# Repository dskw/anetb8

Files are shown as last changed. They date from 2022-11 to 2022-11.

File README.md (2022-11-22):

# Rebuild of the Anet A8 with 2020 extrusions


# Extrusions
* 1x 140mm
* 1x 220mm
* 2x 440mm
* 2x 400mm
* 4x 420mm

# Hardware
* Geetech GT2560 https://www.geeetech.com/wiki/index.php/GT2560
* Buwei 3.3V 1 Channel Relais
* 12V 30A PSU (removed the top plate that holds the fan)
* Noctua NF-A6x25 (60mm)
* RepRapDiscount Full Graphic Smart Controller
* Raspberry Pi 3 B
* deleyCON 1x CAT6a MINI Keystone Jack Modul
* selfmade short 90° usb cables (Pi -> MCU, Pi -> USB Backport)
* selfmade short 90° LAN cable (Pi -> deleyCON)
* 10x15mm drag chain 1 meter
* E3D V6 Clone
* BMG dual gear extruder

All parts are printed in ABS with 5 top/bottom layers and 4 perimeters for maximum stability. (Voron settings)

Additional STLs:
* Printhead: https://www.thingiverse.com/thing:3453289
* Fanduct: https://www.thingiverse.com/thing:2121279 (Mistral_V2.1_Leo_N)

# Printer


# Electronis



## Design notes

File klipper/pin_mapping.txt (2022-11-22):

//
// Limit Switches
//
#define X_MIN_PIN                             22 -> PA0
#define X_MAX_PIN                             24 -> PA2
#define Y_MIN_PIN                             26 -> PA4
#define Y_MAX_PIN                             28 -> PA6
#define Z_MIN_PIN                             30 -> PC7

#define SERVO0_PIN                        11 -> PB5
#define Z_MAX_PIN                         32 -> PC5

//
// Steppers
//
#define X_STEP_PIN                            25 -> PA3
#define X_DIR_PIN                             23 -> PA1
#define X_ENABLE_PIN                          27 -> PA5

#define Y_STEP_PIN                            31 -> PC6
#define Y_DIR_PIN                             33 -> PC4
#define Y_ENABLE_PIN                          29 -> PA7

#define Z_STEP_PIN                            37 -> PC0
#define Z_DIR_PIN                             39 -> PG2
#define Z_ENABLE_PIN                          35 -> PC2

#define E0_STEP_PIN                           43 -> PL6
#define E0_DIR_PIN                            45 -> PL4
#define E0_ENABLE_PIN                         41 -> PG0

#define E1_STEP_PIN                           49 -> PL0
#define E1_DIR_PIN                            47 -> PL2
#define E1_ENABLE_PIN                         48 -> PL1

//
// Temperature Sensors
//
#define TEMP_0_PIN                             8 -> PH5
#define TEMP_1_PIN                             9 -> PH6
#define TEMP_BED_PIN                          10 -> PB4

//
// Heaters / Fans
//
#define HEATER_0_PIN                           2 -> PE4
#define HEATER_1_PIN                           3 -> PE5
#define HEATER_BED_PIN                         4 -> PG5
#define FAN_PIN                              7 -> PH4

//
// Misc. Functions
//
#define SDSS                                  53 -> PB0
#define LED_PIN                               13 -> PB7
#define PS_ON_PIN                             12 -> PB6
#define SUICIDE_PIN                           54  -> PF0 // Must be enabled at startup to keep power flowing
#define KILL_PIN                              -1

#if HAS_WIRED_LCD

  #define BEEPER_PIN                          18 -> PD3

  #if IS_NEWPANEL

    #if ENABLED(MKS_MINI_12864)
      #define DOGLCD_A0                        5
      #define DOGLCD_CS                       21
      #define BTN_EN1                         40
      #define BTN_EN2                         42
    #elif ENABLED(FYSETC_MINI_12864)
      // Disconnect EXP2-1 and EXP2-2, otherwise future firmware upload won't work.
      #define DOGLCD_A0                       20
      #define DOGLCD_CS                       17

      #define NEOPIXEL_PIN                    21
      #define BTN_EN1                         42
      #define BTN_EN2                         40

      #define LCD_RESET_PIN                   16

      #define LCD_CONTRAST_INIT              220

      #define LCD_BACKLIGHT_PIN               -1
    #else
      #define LCD_PINS_RS                     20
      #define LCD_PINS_ENABLE                 17
      #define LCD_PINS_D4                     16
      #define LCD_PINS_D5                     21
      #define LCD_PINS_D6                      5
      #define LCD_PINS_D7                      6
      #define BTN_EN1                         42
      #define BTN_EN2                         40
    #endif

    #define BTN_ENC                           19
    #define SD_DETECT_PIN                     38

  #else                                           // !IS_NEWPANEL

    #define SHIFT_CLK_PIN                     38
    #define SHIFT_LD_PIN                      42
    #define SHIFT_OUT_PIN                     40
    #define SHIFT_EN_PIN                      17

    #define LCD_PINS_RS                       16
    #define LCD_PINS_ENABLE                    5
    #define LCD_PINS_D4                        6
    #define LCD_PINS_D5                       21
    #define LCD_PINS_D6                       20
    #define LCD_PINS_D7                       19

    #if ENABLED(REPRAP_DISCOUNT_FULL_GRAPHIC_SMART_CONTROLLER)
      #define BTN_ENC_EN             LCD_PINS_D7  // Detect the presence of the encoder
    #endif

    #define SD_DETECT_PIN                     -1

  #endif // !IS_NEWPANEL

#endif // HAS_WIRED_LCD

  #define SERVO0_PIN  32

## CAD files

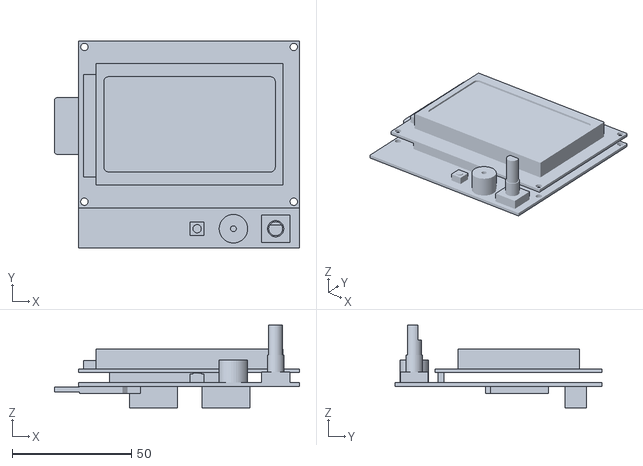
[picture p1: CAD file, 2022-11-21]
source/Full_Graphic_Smart_Controller.STL
102.9 x 86.8 x 34.7

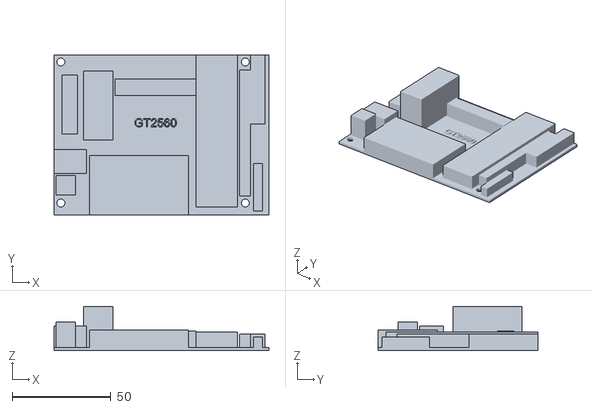
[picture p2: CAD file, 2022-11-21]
source/gt2560.stl
109.0 x 81.0 x 22.5

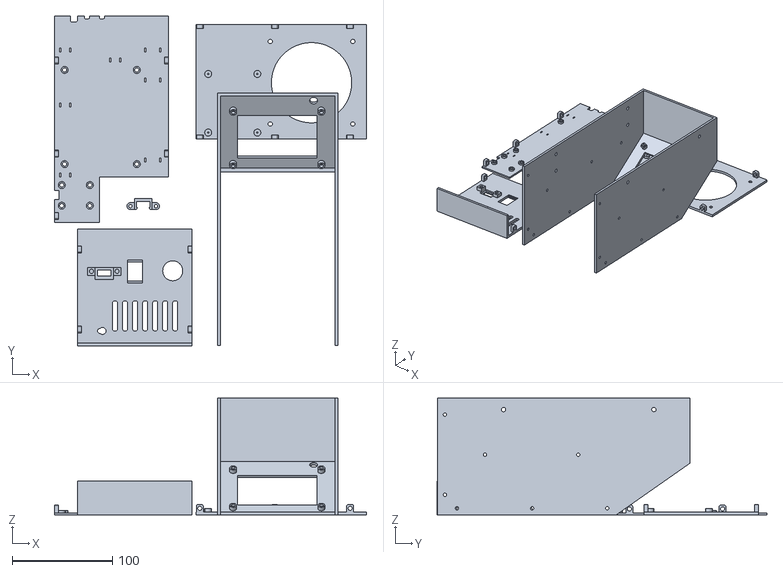
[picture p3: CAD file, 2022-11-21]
stl/anetb8_electronics.stl
311.6 x 329.2 x 116.6

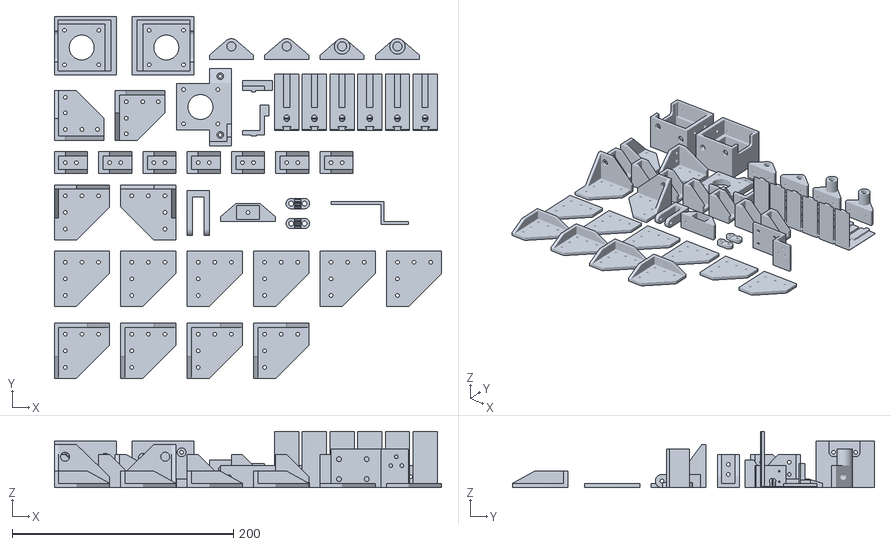
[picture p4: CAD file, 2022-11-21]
stl/anetb8.stl
350.0 x 327.0 x 51.0

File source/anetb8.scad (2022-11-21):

include <libsko.scad>;
//include <SCxxUU-SCxxLUU_v05.scad>

/*
Extrusions
 2x 440
 2x 345 -> 140, 220
 2x 400
 4x 420
 
Rods
 2x 436
 4x 380
 
Lead Screws
2x 345
2x 400
1x 150
*/

RED = [1, 0.3, 0.3];

module Rod(length=10) color("lightgray") render() translate([4, 4, 0]) cylinder(h=length, d=8, $fn=32);

module cornercover() render()
{
    height = 4;
    difference()
    {
        rotate([0,0,-90]) hull()
        {
            cube([50,20,height]);
            cube([20,50,height]);
        }
        translate([25,-10,-0.01]) cylinder(r=M3, h=height+0.02, $fn=32);
        translate([40,-10,-0.01]) cylinder(r=M3, h=height+0.02, $fn=32);
        translate([10,-10,-0.01]) cylinder(r=M3, h=height+0.02, $fn=32);
        translate([10,-25,-0.01]) cylinder(r=M3, h=height+0.02, $fn=32);
        translate([10,-40,-0.01]) cylinder(r=M3, h=height+0.02, $fn=32);
    }
}

module cornercover_foot() render()
{
    height = 4;
    cornercover();
    hull()
    {
        translate([0,-30, 0]) cube([height,30,15]);
        translate([0,-50, 0]) cube([height,40,height]);
    }
    hull()
    {
        translate([0, -4, 0]) cube([30,height,15]);
        translate([0, -4, 0]) cube([50,height,height]);
    }
}

module cornercover_z() render()
{
    height = 4;
    difference()
    {
        union()
        {
            difference()
            {
                rotate([0,0,-90]) hull()
                {
                    cube([50,20,height]);
                    cube([20,50,height]);
                }
                translate([25,-10,-0.01]) cylinder(r=M3, h=height+0.02, $fn=32);
                translate([40,-10,-0.01]) cylinder(r=M3, h=height+0.02, $fn=32);
                translate([10,-10,-0.01]) cylinder(r=M3, h=height+0.02, $fn=32);
                translate([10,-25,-0.01]) cylinder(r=M3, h=height+0.02, $fn=32);
                translate([10,-40,-0.01]) cylinder(r=M3, h=height+0.02, $fn=32);
            }

            if(1) hull()
            {
                translate([0, -height, -35]) cube([20,height,35]);
                translate([0, -height, -10+height]) cube([50,height,10]);
            }
            hull()
            {
                translate([0, -height, -35]) cube([height,height,35]);
                translate([0, -30, 0]) cube([height,10,1]);
            }
        }
        translate([9.75,0.01,-24]) rotate([90,0,0]) cylinder(r=4.1, h=height+0.02, $fn=32);
    }
}

module cornerbrace() render()
{
    height = 4;
    difference()
    {
        union()
        {
            cube([30,height,20]);
            cube([height,30,20]);
            hull()
            {
                cube([30,10,height]);
                cube([10,30,height]);
            }
            translate([0,0,16]) hull()
            {
                cube([30,10,height]);
                cube([10,30,height]);
            }
        }
        translate([10,height+0.01,10-0.01]) rotate([90,0,0]) cylinder(r=M3, h=height+0.02, $fn=32);
        translate([20,height+0.01,10-0.01]) rotate([90,0,0]) cylinder(r=M3, h=height+0.02, $fn=32);
        translate([-0.01,12,10-0.01]) rotate([0,90,0]) cylinder(r=M3, h=height+0.02, $fn=32);
        translate([-0.01,21,10-0.01]) rotate([0,90,0]) cylinder(r=M3, h=height+0.02, $fn=32);
    }
}

module cornerbrace_zb() render()
{
    height = 4;
    difference()
    {
        union()
        {
            hull()
            {
                cube([45,height,20]);
                cube([20,height,45]);
            }
            hull()
            {
                cube([height,30,20]);
                cube([height,height,45]);
            }
            hull()
            {
                cube([45,10,height]);
                cube([10,30,height]);
            }
        }
        translate([10,height+0.01,10-0.01]) rotate([90,0,0]) cylinder(r=M3, h=height+0.02, $fn=32);
        translate([25,height+0.01,10-0.01]) rotate([90,0,0]) cylinder(r=M3, h=height+0.02, $fn=32);
        translate([39,height+0.01,10-0.01]) rotate([90,0,0]) cylinder(r=M3, h=height+0.02, $fn=32);
        translate([10,height+0.01,39-0.01]) rotate([90,0,0]) cylinder(r=M3, h=height+0.02, $fn=32);
        translate([10,height+0.01,25-0.01]) rotate([90,0,0]) cylinder(r=M3, h=height+0.02, $fn=32);
        translate([-0.01,12,10-0.01]) rotate([0,90,0]) cylinder(r=M3, h=height+0.02, $fn=32);
        translate([-0.01,23,10-0.01]) rotate([0,90,0]) cylinder(r=M3, h=height+0.02, $fn=32);
    }
}

module MotorMountZ() render()
{
    if(1) difference()
    {
        translate([-10,-7,0]) cube([56,53,42]);
        // side screws
        translate([-5.16,0.1,-0.01]) cube([6.01,42.1,20.01]);
        translate([-12,10,10]) rotate([0,90,0]) cylinder(h=10, r=M3, $fn=32);
        translate([-12,30,10]) rotate([0,90,0]) cylinder(h=10, r=M3, $fn=32);
        hull(){
            translate([40,10,10]) rotate([0,90,0]) cylinder(h=10, r=4, $fn=32);
            translate([40,30,10]) rotate([0,90,0]) cylinder(h=10, r=4, $fn=32);
            translate([40,10,-10]) rotate([0,90,0]) cylinder(h=10, r=4, $fn=32);
            translate([40,30,-10]) rotate([0,90,0]) cylinder(h=10, r=4, $fn=32);
        }
        // back screw
        translate([-5.16,-4,-0.01]) cube([47.61,5,20.01]);
        translate([0,0,15]) rotate([90,0,0]) cylinder(h=10, r=M3, $fn=32);
        translate([35,0,10]) rotate([90,0,0]) cylinder(h=10, r=M3, $fn=32);
        translate([0,50,15]) rotate([90,0,0]) cylinder(h=10, r=4, $fn=32);
        translate([35,50,10]) rotate([90,0,0]) cylinder(h=10, r=4, $fn=32);
        // motor
        union()
        {
            translate([-0.05,-0.3,-6.3]) cube([42+0.6,42+0.6,45]);
            translate([21.25,21,36.99]) cylinder(h=10, d=22.5, $fn=64);
            translate([42/2 - 31/2  +0.25,42/2 - 31/2,36.99]) {
                translate([0,0,0]) cylinder(r=M3, h=10, $fn=32);
                translate([31,0,0]) cylinder(r=M3, h=10, $fn=32);
                translate([31,31,0]) cylinder(r=M3, h=10, $fn=32);
                translate([0,31,0]) cylinder(r=M3, h=10, $fn=32);
            }
        }
        // rod holder
        translate([-0.25,20.75,40]) rotate([0,0,0]) cylinder(r=4.2, h=10, $fn=32);
    }
    
    if (0) 
    {
        translate([0.25,-0.0,-9.5])difference()
        {
            union()
            {
                color("gray") cube([42,42,48]);
                color("lightgray") translate([21,21,48]) cylinder(d=22, h=2, $fn=64);
            }
        
            color("red") translate([42/2 - 31/2,42/2 - 31/2,48-4.5]) {
                translate([0,0,0]) cylinder(r=M3, h=5, $fn=32);
                translate([31,0,0]) cylinder(r=M3, h=5, $fn=32);
                translate([31,31,0]) cylinder(r=M3, h=5, $fn=32);
                translate([0,31,0]) cylinder(r=M3, h=5, $fn=32);
            }
        }
    }
}

module MotorMountY() render()
{
    difference()
    {
        union()
        {
            translate([-10,4.5,8.5]) cube([20,42,41]);
            translate([-10,-10,0]) cube([8,55.5,20]);
            hull()
            {
                translate([-10,45,0]) cube([8,2,20]);
                translate([-10,50,0]) cube([4,10,20]);
            }
            translate([-10,-10,0]) cube([25,4,20]);
            hull()
            {
                translate([-10,-10,0]) cube([25,8,4]);
                translate([-10,-10,0]) cube([8,20,4]);
            }
        }
        translate([7,-5,10]) rotate([90,0,0]) cylinder(h=10, r=M3, $fn=32);
        translate([-6,0,10]) rotate([0,90,0]) cylinder(h=15, r=3, $fn=32);
        translate([-15,0,10]) rotate([0,90,0]) cylinder(h=10, r=M3, $fn=32);
        translate([-6,53,10]) rotate([0,90,0]) cylinder(h=15, r=3, $fn=32);
        translate([-15,53,10]) rotate([0,90,0]) cylinder(h=10, r=M3, $fn=32);
        
        // motor
        translate([35.0,4.5,7.2]) rotate([0,-90,0]) union()
        {
            translate([-0.1,-0.1,-0.01]) cube([42.7,42.7,37.01]);
            translate([-8,20.75 - 7.5,-0.01]) cube([10,15,10.01]);
            translate([20.75,20.75,36.99]) cylinder(h=10, d=22.5, $fn=64);
            
            screwhole = 5-0.2;
            
            // br
            translate([5,5.5,36.99]) cylinder(h=screwhole, r=M3, $fn=32);
            translate([5,5.5,40.99]) cylinder(h=10, r=3, $fn=32);
            // tr
            translate([36,5.5,36.99]) cylinder(h=screwhole, r=M3, $fn=32);
            translate([36,5.5,40.99]) cylinder(h=10, r=3, $fn=32);
            // bl
            translate([5,36.5,36.99]) cylinder(h=screwhole, r=M3, $fn=32);
            translate([5,36.5,40.99]) cylinder(h=10, r=3, $fn=32);
            // tl
            translate([36,36.5,36.99]) cylinder(h=screwhole, r=M3, $fn=32);
            translate([36,36.5,40.99]) cylinder(h=10, r=3, $fn=32);
        }
    }
}
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

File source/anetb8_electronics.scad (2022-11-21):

include <libsko.scad>;

RED = [0.5, 0.5, 0.5];


/*

~~~~~~~~~~ TODO ~~~~~~~~~~
 * RPi power cable

*/

// case
module LackCase()
{
    color("white") render()
    {
        translate([0,0,0]) cube([550,550,50]);
        translate([0,0,800]) cube([550,550,50]);
        
        translate([0,0,0]) cube([50,50,400*2]);
        translate([500,0,0]) cube([50,50,400*2]);
        translate([500,500,0]) cube([50,50,400*2]);
        translate([0,500,0]) cube([50,50,400*2]);
    }
    
    color("white", 0.2) render()
    {
        translate([50,5,50]) cube([450,5,400*2 - 50]);
        translate([5,50,50]) cube([5,450,400*2 - 50]);
        translate([550-10,50,50]) cube([5,450,400*2 - 50]);
        translate([50,550-10,50]) cube([450,5,400*2 - 50]);
    }
}

module Powersupply() color("silver") render()
{
    width = 114;
    length = 215;
    height = 50;
    difference()
    {
        cube([width,length,height]);
        translate([1.7,-1,7.5 + 1]) cube([width - 1.7*2,18.5 + 1,42.5]);
        translate([38,165,height-3]) cylinder(d=60, h=5, $fn=64);
        translate([-2,32,11.5]) rotate([0,90,0]) cylinder(r=M4, h=5, $fn=32);
        translate([-2,182,11.5]) rotate([0,90,0]) cylinder(r=M4, h=5, $fn=32);
        translate([width-2,32,11.5]) rotate([0,90,0]) cylinder(r=M4, h=5, $fn=32);
        translate([width-2,182,11.5]) rotate([0,90,0]) cylinder(r=M4, h=5, $fn=32);
        translate([width-2,32,36]) rotate([0,90,0]) cylinder(r=M4, h=5, $fn=32);
        translate([width-2,182,36]) rotate([0,90,0]) cylinder(r=M4, h=5, $fn=32);
    }
    translate([18,0,5]) cube([90,15.5,15.5]);
    translate([50,0,14]) rotate([90,0,0]) cylinder(d=6.6, h=30, $fn=32);
    translate([90,0,14]) rotate([90,0,0]) cylinder(d=6.6, h=30, $fn=32);
}

module MountPi(r=M2, h=10, $fn=32) translate([4.87+M2, 3.7+M2, 0])
{
    cylinder(r=r, h=h);
    translate([58.5,0,0]) cylinder(r=r, h=h);
    translate([58.5,49,0]) cylinder(r=r, h=h);
    translate([0,49,0]) cylinder(r=r, h=h);
}
module RaspberryPi() color("green")
{
    import("Raspberry_Pi_3_Light_Version.STL");
}


module Display() color("darkred") render()
{
    import("Full_Graphic_Smart_Controller.STL");
}


module Fan() color([244/255, 224/255, 198/255]) render()
{
    difference()
    {
        roundcube([92,92,15], 5);
        translate([2.6+M4,2.6+M4,-1]) cylinder(r=M4, h=20, $fn=32);
        translate([92 - 2.6 - M4,2.6+M4,-1]) cylinder(r=M4, h=20, $fn=32);
        translate([92 - 2.6 - M4,92 - 2.6 - M4,-1]) cylinder(r=M4, h=20, $fn=32);
        translate([2.6 + M4,92 - 2.6 - M4,-1]) cylinder(r=M4, h=20, $fn=32);
        translate([92/2,92/2,-1]) cylinder(d=89, h=20, $fn=128);
    }
}


module MountBoard(r=M3, h=5, $fn=32) translate([1.3+M3, 3.6+M3, 0]) 
{
    cylinder(r=r, h=h);
    translate([94,72,0]) cylinder(r=r, h=h);
    translate([0,72,0]) cylinder(r=r, h=h);
    translate([94,0,0]) cylinder(r=r, h=h);
}
module Board() color("white")
{
    import("gt2560.stl");
    difference()
    {
        translate([0, 0, -1]) cube([109,81, 1]);
        translate([0, 0, -2]) MountBoard(h=6);
    }
}


module MountRelay(r=M3, h=5, $fn=32) translate([1.2+M3, 0.75+M3, 0]) 
{
    cylinder(r=r, h=h);
    translate([20.5,28,0]) cylinder(r=r, h=h);
    translate([20.5,0,0]) cylinder(r=r, h=h);
    translate([0,28,0]) cylinder(r=r, h=h);
}
module Relay() color("lightblue") render()
{
    difference()
    {
        cube([26.5, 33.5, 4]);
        translate([0, 0, -1]) MountRelay(h=6);
    }
    translate([5.5,2,0]) cube([15.5, 26.5, 19]);
    translate([5.5,33.5,5]) cube([1, 4.5, 1]);
    translate([7.75,33.5,5]) cube([1, 4.5, 1]);
    translate([10,33.5,5]) cube([1, 4.5, 1]);
    translate([5.5,32.5,4]) cube([5.5, 1, 2]);
}


module USBHolder() color(RED) render()
{
    difference()
    {
        $fn=32;
        union()
        {
            translate([0,0,0]) cube([17.5,9,11]);
            hull()
            {
                translate([-4,3,7.5]) rotate([90,0,0]) cylinder(r=3.5, h=3);
                translate([21.5,3,7.5]) rotate([90,0,0]) cylinder(r=3.5, h=3);
            }
        }
        translate([2,-1,3]) cube([13.5,11,10]);
        translate([-4,9.5,7.5]) rotate([90,0,0]) cylinder(r=M3, h=12);
        translate([21.5,9.5,7.5]) rotate([90,0,0]) cylinder(r=M3, h=12);
    }
    translate([2,0,11]) rotate([-90,0,0]) linear_extrude(9) polygon([[0,0],[0,2],[1,2],[0,0]]);
    translate([15.5,0,11]) mirror([1,0,0]) rotate([-90,0,0]) linear_extrude(9) polygon([[0,0],[0,2],[1,2],[0,0]]);
}


module CaseTop() color(RED) render() 
{
    difference()
    {
        union()
        {
            // top
            translate([-0.2,75.723,113.621]) cube([114.4,170.28,3]);

            // raspberrypi mount
            if (1) translate([-0.0, 82.8, 110.3]) difference()
            {
                MountPi(r=3.5, h=3.5);
                translate([0, 0, -1]) MountPi(r=0.75);
            }
        }
        
        // fan mount
        translate([10, 145, 105])
        {
            translate([2.6+M4,2.6+M4,-1]) cylinder(r=M4, h=20, $fn=32);
            translate([92 - 2.6 - M4,2.6+M4,-1]) cylinder(r=M4, h=20, $fn=32);
            translate([92 - 2.6 - M4,92 - 2.6 - M4,-1]) cylinder(r=M4, h=20, $fn=32);
            translate([2.6 + M4,92 - 2.6 - M4,-1]) cylinder(r=M4, h=20, $fn=32);
            translate([92/2,92/2,-1]) cylinder(d=80, h=20, $fn=128);
        }
    }
    for(y=[76:75:240])
    {
        translate([0,y,116]) rotate([0,90,0]) difference()
        {
            roundcube([10,7,4]);
            translate([6,3.5,-1]) cylinder(d=HI_M3*2, h=6, $fn=32);
        }
        translate([110,y,116]) rotate([0,90,0]) difference()
        {
            roundcube([10,7,4]);
            translate([6,3.5,-1]) cylinder(d=HI_M3*2, h=6, $fn=32);
        }
    }
}
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

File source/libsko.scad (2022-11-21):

include <path_extrude.scad>;

M2=1.4;
M3=1.7;
M4=2.2;
// heated inserts
HI_M3=2.1;

module nut_M3() {
    cylinder(2,3.2,3.2,$fn=6);
}

module fillet(r, h) {
    translate([r / 2, r / 2, 0])
    difference() {
        cube([r + 0.01, r + 0.01, h], center = true);

        translate([r/2, r/2, 0])
            cylinder(r = r, h = h + 1, center = true);

    }
}

module roundcube(dim, r=2, $fn=32) {
    hull() {
        translate([r,r,0]) cylinder(dim[2], r, r);
        translate([dim[0]-r, r,0]) cylinder(dim[2], r, r);
        translate([r,dim[1]-r,0]) cylinder(dim[2], r, r);
        translate([dim[0]-r, dim[1]-r,0]) cylinder(dim[2], r, r);
    }
}

module Extrusion(length = 10, color = [0.2, 0.2, 0.2])
{
    color(color) render() difference()
    {
        linear_extrude(length)
        polygon([
            // corner
            [0,1], [1,0],
            // cut in
            [7, 0], [7, 1.6], [4, 1.6], [4, 3], [6.5, 5.5],
            [13.5, 5.5], [16, 3], [16, 1.6], [13, 1.6], [13, 0],
            // corner
            [19,0], [20,1],
            // cut in
            [20,7], [18.4, 7], [18.4, 4], [17, 4], [14.5, 6.5],
            [14.5, 13.5], [17, 16], [18.4, 16], [18.4, 13], [20, 13],
            // corner
            [20,19], [19,20],
            // cut in
            [13, 20], [13, 18.4], [16, 18.4], [16, 17], [13.5, 14.5],
            [6.5, 14.5], [4, 17], [4, 18.4], [7, 18.4], [7, 20],
            // corner
            [1,20], [0,19],
            // cut in
            [0, 13], [1.6, 13], [1.6, 16], [3, 16], [5.5, 13.5],
            [5.5, 6.5], [3, 4], [1.6, 4], [1.6, 7], [0, 7],
            // loop end
            [0,1]
        ]);
        translate([10, 10, -0.01]) cylinder(h=length + 0.02,d=5.5, $fn = 32);
    }
}

module square_hollow(dim, wall=0.5) {
    h = dim[0];
    w = dim[1];
    polygon(points=[
        [0,wall],
        [0,0],
        [h,0],
        [h,w],
        [0,w],
        [0,wall],
        [wall,wall],
        [wall,w-wall],
        [h-wall,w-wall],
        [h-wall,wall]
    ]);
}

module square_dome(size, dome=3, inner=false, wall=0.5) {
    w = size[1];
    h = size[0];
    p=2;
    if (inner) {
        polygon(points=[
            [wall,wall],
            [wall,w-wall+0.15],
            [h/p,w-wall+dome-wall/p+0.15],
            [h-wall,w-wall+0.15],
            [h-wall,wall]
        ]);
    } else {
        polygon(points=[
            [0,wall],
            [0,0],
            [h,0],
            [h,w],
            [h/p,w+dome],
            [0,w],
            [0,wall],
        ]);
    }
}

module PTFECoupling()
{
    render() difference() {
        union() {
            cylinder(r=5.8/2, h=4.5);
            translate([0, 0, 4.5]) cylinder(r=4, h=1.5);
            translate([0, 0, 6]) cylinder(r=11.45/2, h=10.2, $fn=6);
            translate([0, 0, 16.2]) cylinder(r=4, h=1.2);
            translate([0, 0, 17.4]) cylinder(r=2.5, h=1.2);
            translate([0, 0, 18.6]) cylinder(r=11.45/2, h=1.2);
        }
        translate([0, 0, -0.01]) cylinder(r=2.6/2, h=15);
        translate([0, 0, 10]) cylinder(r=4.3/2, h=10);
    }
}

module Fan(size=40,depth=10) {
    difference() {
        cube([size, depth, size]);
        translate([size/2,depth+1,size/2]) rotate([90,0,0]) cylinder(depth+2,size/2-1,size/2-1, $fn=128);
        translate([M3 + 1.5, depth+1, M3 + 1.5]) rotate([90,0,0]) cylinder($fn=32, r=M3, h=depth+2);
        translate([M3 + 1.5, depth+1, size - M3 - 1.5]) rotate([90,0,0]) cylinder($fn=32, r=M3, h=depth+2);
        translate([size -M3 -1.5, depth+1, M3 + 1.5]) rotate([90,0,0]) cylinder($fn=32, r=M3, h=depth+2);
        translate([size -M3 -1.5, depth+1, size - M3 - 1.5]) rotate([90,0,0]) cylinder($fn=32, r=M3, h=depth+2);
    }
    translate([size/2,depth,size/2]) rotate([90,0,0]) cylinder(depth,size/5,size/5, $fn=128);
    translate([size/2,depth/2,size/2]) for(r=[0:40:360]) rotate([0,r,0]) 
        translate([size/3,0,0]) rotate([60,0,0]) scale([1,0.5,1]) rotate([0,0,180]) cylinder(1,size/4,size/4, $fn=3);
}

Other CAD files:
source/path_extrude.scad

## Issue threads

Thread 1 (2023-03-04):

wrong pin mapping

speedbirdone, 2023-03-04:
pin list in pin_mapping.txt is correct, but mapped to the wrong alias pins. Check against https://github.com/Klipper3d/klipper/blob/master/config/sample-aliases.cfg

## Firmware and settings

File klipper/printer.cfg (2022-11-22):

[include mainsail.cfg]

# This file contains common pin mappings for the Geeetech GT2560
# board. GT2560 board uses a firmware compiled for the AVR
# atmega2560.
#
# based on: https://github.com/Klipper3d/klipper/blob/master/config/generic-gt2560.cfg
# pin mapping from Marlin: https://github.com/MarlinFirmware/Marlin/blob/ba8d43d70efc03ee4bcf6bcbb8b102275740ea4f/Marlin/src/pins/mega/pins_GT2560_REV_A.h
# mapped to pins from klipper: https://github.com/Klipper3d/klipper/blob/master/config/sample-aliases.cfg

# See docs/Config_Reference.md for a description of parameters.

[mcu]
serial: /dev/serial/by-id/usb-FTDI_FT232R_USB_UART_A9070TIG-if00-port0

[mcu rpi]
serial: /tmp/klipper_host_mcu

[adxl345]
cs_pin: rpi:None

[resonance_tester]
accel_chip: adxl345
probe_points:
    110, 110, 20  # an example

[input_shaper]
shaper_freq_x: 23
shaper_type_x: mzv
shaper_freq_y: 54.6
shaper_type_y: 3hump_ei

[temperature_sensor pi]
sensor_type: temperature_host
min_temp: 0
max_temp: 90

[printer]
kinematics: cartesian
max_velocity: 200
max_accel: 1500
max_z_velocity: 20
max_z_accel: 500


[stepper_x]
step_pin: PA3
dir_pin: !PA1
enable_pin: !PA5
microsteps: 16
rotation_distance: 32
endstop_pin: ^!PA0
position_min: -38
position_max: 220
position_endstop: -38
homing_speed: 30

[stepper_y]
step_pin: PC6
dir_pin: !PC4
enable_pin: !PA7
microsteps: 16
rotation_distance: 32
endstop_pin: ^!PA6
position_min: -18
position_max: 220
position_endstop: -18
homing_speed: 30

[stepper_z]
step_pin: PC0
dir_pin: PG2
enable_pin: !PC2
microsteps: 16
rotation_distance: 8
endstop_pin: probe:z_virtual_endstop
#position_endstop: 0
position_max: 200
position_min: -3.0

[extruder]
step_pin: PL6
dir_pin: PL4
enable_pin: !PG0
microsteps: 16
rotation_distance: 21.64 # 22.95
gear_ratio: 3:1
nozzle_diameter: 0.4
filament_diameter: 1.750
heater_pin: PE4
sensor_type: Generic 3950
sensor_pin: PK0
min_temp: 0
max_temp: 250
pressure_advance: 0.13
#control: pid
#pid_kp: 29.800
#pid_ki: 1.774
#pid_kd: 125.159

[verify_heater extruder]
max_error: 240
check_gain_time: 60
hysteresis: 10
heating_gain: 1

[heater_bed]
heater_pin: PG5
sensor_type: Generic 3950
sensor_pin: PK2
min_temp: 0
max_temp: 85
#control: pid
#pid_kp: 63.041
#pid_ki: 2.898
#pid_kd: 342.787

[fan]
pin: PH4
max_power: 1.0

[bltouch]
sensor_pin: ^PC7
control_pin: PB5
x_offset: 37
y_offset: 4
#z_offset: 0
samples: 3

[safe_z_home]
home_xy_position: 20, 20 # Change coordinates to the center of your print bed
speed: 50
z_hop: 10                 # Move up 10mm
z_hop_speed: 5

[bed_mesh]
speed: 120
horizontal_move_z: 10
mesh_min: 20, 15
mesh_max: 200, 200
probe_count: 3, 3

[display]
lcd_type: st7920
cs_pin: PE3
sclk_pin: PH1
sid_pin: PH0
encoder_pins: ^PL7, ^PG1
click_pin: ^!PD2

[output_pin BEEPER_pin]
pin: PD3
pwm: True
value: 0
shutdown_value: 0
cycle_time: 0.001
scale: 1000

[respond]

[idle_timeout]
gcode:
	{% if printer.pause_resume.is_paused %}
	  M117 "timeout ignored because printer state == paused."
	{% else %}
	  {% if (printer.toolhead.homed_axes == 'xyz' and printer.toolhead.axis_maximum.z > (printer.toolhead.position.z + 20)) %}
		G91
		G0 Z10 F600
		G90
		G0 X110 Y110 F2000
	  {% endif %}
	  M84
      M140 S0
      M104 S0
      M106 S0
	  UPDATE_DELAYED_GCODE ID=DELAYED_PRINTER_OFF DURATION=60
	{% endif %}

######################################################################
# Custom Macros
######################################################################
	
[gcode_macro POWER_OFF_PRINTER]
gcode =
  {action_call_remote_method("set_device_power",
                             device="psu",
                             state="off")}
	
[gcode_macro POWER_ON_PRINTER]
gcode =
  {action_call_remote_method("set_device_power",
                             device="psu",
                             state="on")}
                             
[delayed_gcode DELAYED_PRINTER_OFF]
initial_duration = 0.
gcode =
  {% if printer.idle_timeout.state == "Idle" %}
    {% if printer["extruder"].temperature > 50 %}
      UPDATE_DELAYED_GCODE ID=DELAYED_PRINTER_OFF DURATION=60
    {% else %}
      POWER_OFF_PRINTER
    {% endif %}
  {% else %}
    M118 Printer not idle, cancelled PRINTER_OFF.
  {% endif %}

# Replace the slicer's custom start and end g-code scripts with
# START_PRINT and END_PRINT.

[gcode_macro START_PRINT]
gcode:
    {% set BED_TEMP = params.BED_TEMP|default(60)|float %}
    {% set EXTRUDER_TEMP = params.EXTRUDER_TEMP|default(220)|float %}
    # Start bed heating
    M140 S{BED_TEMP}
    # Use absolute coordinates
    G90
    # Reset the G-Code Z offset (adjust Z offset if needed)
    ;SET_GCODE_OFFSET Z=0.0
    # Home the printer
    G28
    BED_MESH_CALIBRATE ; Auto bed-level (BL-Touch)
    # Move the nozzle near the bed
    G1 Z5 F3000
    # Move the nozzle very close to the bed
    ;G1 Z0.15 F300
    # Wait for bed to reach temperature
    M190 S{BED_TEMP}
    # Set and wait for nozzle to reach temperature
    M109 S{EXTRUDER_TEMP}
    G90
    G1 X10 Y1 Z0.3
    G1 X70 Y1 Z0.3 E10 F300
    

[gcode_macro END_PRINT]
gcode:
    # Turn off bed, extruder, and fan
    M140 S0
    M104 S0
    M106 S0
    # Move nozzle away from print while retracting
    G91
    ;G1 X-2 Y-2 E-3 F300
    # Raise nozzle by 10mm
    G1 Z10 F3000
    G28 X0  ; home X axis
    G90
    # Disable steppers
    M84

[gcode_macro M300]
gcode:  
        {% set v_frequency = params.S|default(1000)|int %}
        {% set v_duraton = params.P|default(100)|int %}
        SET_PIN PIN=BEEPER_pin VALUE={v_frequency}
        G4 P{v_duraton}
        SET_PIN PIN=BEEPER_pin VALUE=0

[gcode_macro CENTER]
gcode:  
        G0 X110 Y110 Z10



#*# <---------------------- SAVE_CONFIG ---------------------->
#*# DO NOT EDIT THIS BLOCK OR BELOW. The contents are auto-generated.
#*#
#*# [extruder]
#*# control = pid
#*# pid_kp = 25.469
#*# pid_ki = 1.179
#*# pid_kd = 137.530
#*#
#*# [heater_bed]
#*# control = pid
#*# pid_kp = 70.726
#*# pid_ki = 1.010
#*# pid_kd = 1238.592
#*#
#*# [bltouch]
#*# z_offset = 2.269
#*#
#*# [bed_mesh default]
#*# version = 1
#*# points =
#*# 	0.005833, -0.050833, 0.010833
#*# 	-0.114167, -0.295000, -0.245833
#*# 	0.100000, -0.238333, -0.290833
#*# x_count = 3
#*# y_count = 3
#*# mesh_x_pps = 2
#*# mesh_y_pps = 2
#*# algo = lagrange
#*# tension = 0.2
#*# min_x = 20.0
#*# max_x = 200.0
#*# min_y = 15.0
#*# max_y = 200.0
